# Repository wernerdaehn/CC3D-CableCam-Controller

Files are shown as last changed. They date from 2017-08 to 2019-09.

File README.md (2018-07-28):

[LICENSE](LICENSE)

# CableCam-Controller

**A CableCam Controller to allow smooth movements and automatic braking near the end points of the rope.**

## Goals

The most simple way to control a cablecam is by connecting the RC receiver to the motor controller (=ESC, electronic speed controller) and control it like a RC car.
But this has multiple limitations this CableCam Controller tries to solve:

1. The CableCam might crash into the start- or endpoint by accident. Would be much nicer if the CableCam calculates the required braking distance constantly and does engage the brake automatically. This way it stops no matter of the user input.
2. A smooth acceleration/deceleration makes the videos look more cinematic. Even when the stick is pushed forward at once, the CableCam should accelerate slowly instead of the wheel spinning damaging the rope.
3. A speed limiter to protect the CableCam from going too fast and for constant speed travels during filming.
4. Preprogram movement patterns and the Cablecam repeats them on request.

To achieve that, the CableCam controller sits between the receiver and the motor controller and acts as a governour of the receiver input. If, for example, the user did push the stick forward from neutral to max within a second, the CableCam Controller rather increases the stick position slowly. For speed and positional input the controller is connected to two hall sensors on one of the running wheels.

MCU used is [STM32F405RG](http://www.st.com/en/microcontrollers/stm32f405rg.html) 
Board used: Any CC3D Revolution or clone, e.g. the [Flip 32 F4](https://github.com/iNavFlight/inav/blob/master/docs/Board%20-%20Airbot%20F4%20and%20Flip32%20F4.md) which can be bought at various shops for little money [(here?)](https://www.rctech.de/flip32-f4-flight-controller.html).

See all videos at: https://www.youtube.com/channel/UCTLw_Boy24qAhuygCyIOzyw 

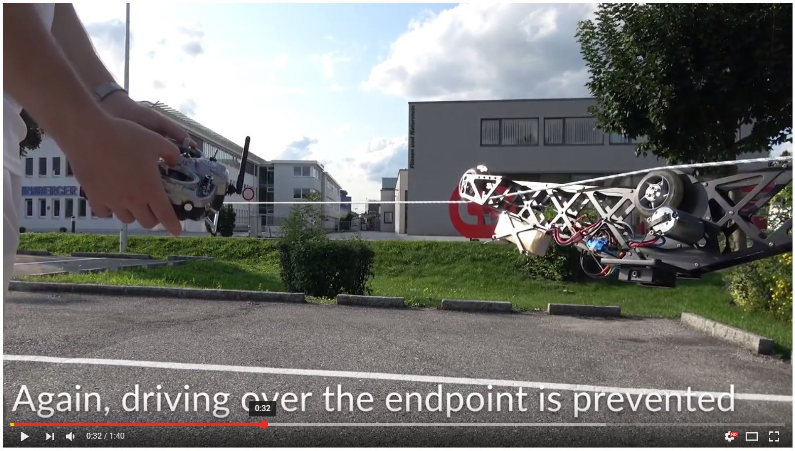
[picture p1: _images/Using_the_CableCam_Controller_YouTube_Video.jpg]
Using the CableCam Controller (https://youtu.be/ohzvkKzsO8Q "Using the CableCam Controller")


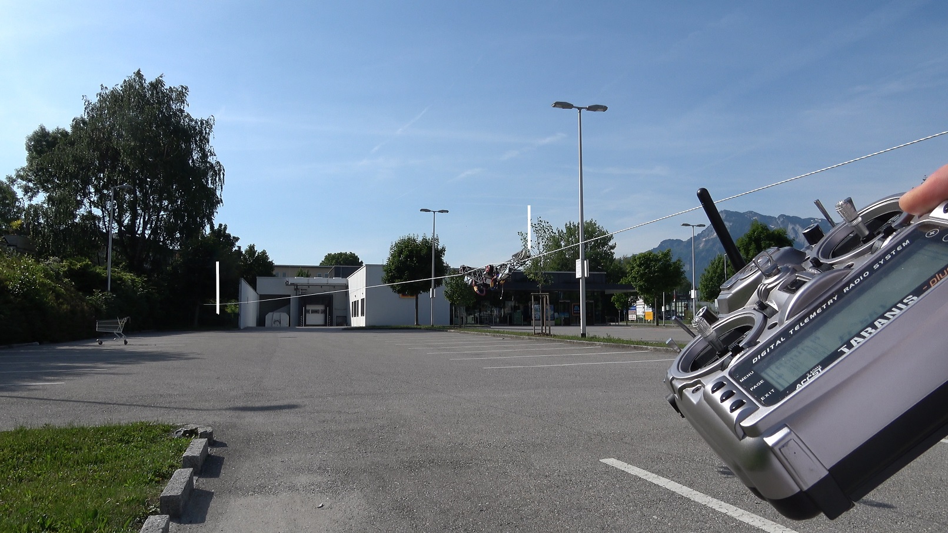
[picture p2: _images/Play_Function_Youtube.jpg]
The Play function (https://www.youtube.com/watch?v=D3UhXKbMN38 "The Play function")


If the stick is pushed full forward, the cablecam will start accelerating with the maximum allowed value instead until the maximum allowed speed is reached. This speed is held until it starts to decelerate with the same acceleration level so that it reaches the end point at zero speed.

Using the speed dial the maximum speed can be configured. And with the accel dial the steepness of the linear acceleration curve.

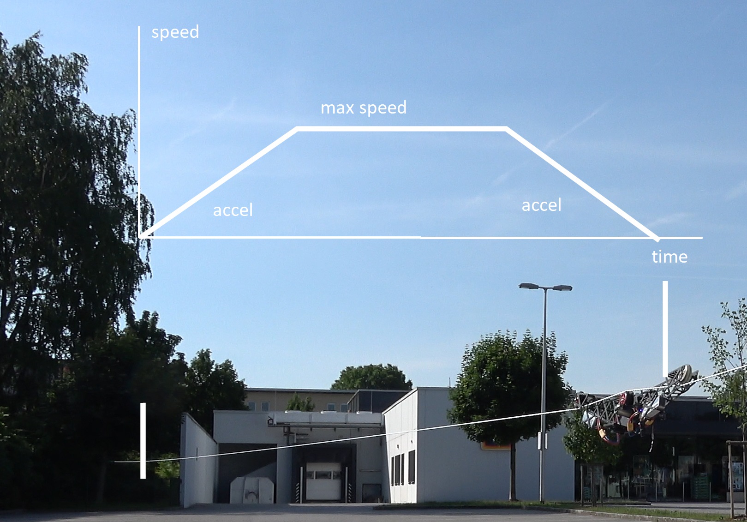
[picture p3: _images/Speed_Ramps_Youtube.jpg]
Speed Ramps (https://www.youtube.com/watch?v=Usq5xiH9H7Y)


## Setup

1. [Flashing the Firmware](docs/Step%201%20-%20Flashing%20the%20Firmware.md)
2. [Connecting the board](docs/Step%202%20-%20Connect%20to%20the%20board.md) to the computer for first tests and settings
3. Choosing the receiver
   1. [SBus](docs/Step%203a%20-%20Receiver%20Input%20SBus.md)
   2. [SumPPM](docs/Step%203b%20-%20Receiver%20Input%20SumPPM.md)
4. [Assigning input channels](docs/Step%203b%20-%20Receiver%20Input%20SumPPM.md)
5. Connecting the motor controller (ESC)
   1. Using a [servo signal to control the ESC](docs/Step%205a%20-%20Regular%20ESC.md)
   2. Using the [VESC6 as motor controller](docs/Step%205b%20-%20VESC%20as%20motor%20controller.md)
6. [Connecting the position sensor](docs/Step%206%20-%20Connecting%20the%20Position%20Sensor.md)
7. [Limiters](docs/Step%207%20-%20Limiters.md)
8. [Endpoints](docs/Step%208%20-%20Endpoints.md)
9. [Aux Channel](docs/Step%209%20-%20Aux%20channel.md) (optional)
10. [Bluetooth](docs/Step%2010%20-%20Bluetooth.md) (optional)
11. [Play Function](docs/Step%2011%20-%20Play.md) (optional)

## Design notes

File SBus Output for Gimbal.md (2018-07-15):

# SBus Output

In order to control the gimbal there are multiple options

- A second remote like the one that comes with the Ronin itself.
- A second receiver in case the RC sender supports two receivers being bound to it simultaniously. FrSky Taranis does.
- Split the SBus signal from the receiver.
- CableCam Controller itself does generate the SBus signal for the Gimbal.

The latter is described here. The longterm goal is to enable the cablecam controller fully automatic movements including gimbal. Repeat travel patterns, keep the camera pointing to a POI regardeless of where it is at the moment and things like that.

At the moment however the SBus input channels are mapped to output channels and a SBus signal is created for that.

## Hardware

#### MCU Pins used

| Function | MCU Pin | MCU Function | Connector Pin | Flip32 F4  |
| --- | --- | --- | --- | --- |
| SBus Out (non-inverted) | PC7 | USART6_TX | FlexIO Pin8 | CH6/TX6/J6 |
| GND | | | FlexIO Pin1 | GND/J2 |

Attention: **Do not connect the +5V line** with the board! Since both, gimbal and board do provide 5V power, it could cause damage. Would be like connecting two batteries with each other.

#### Pinout

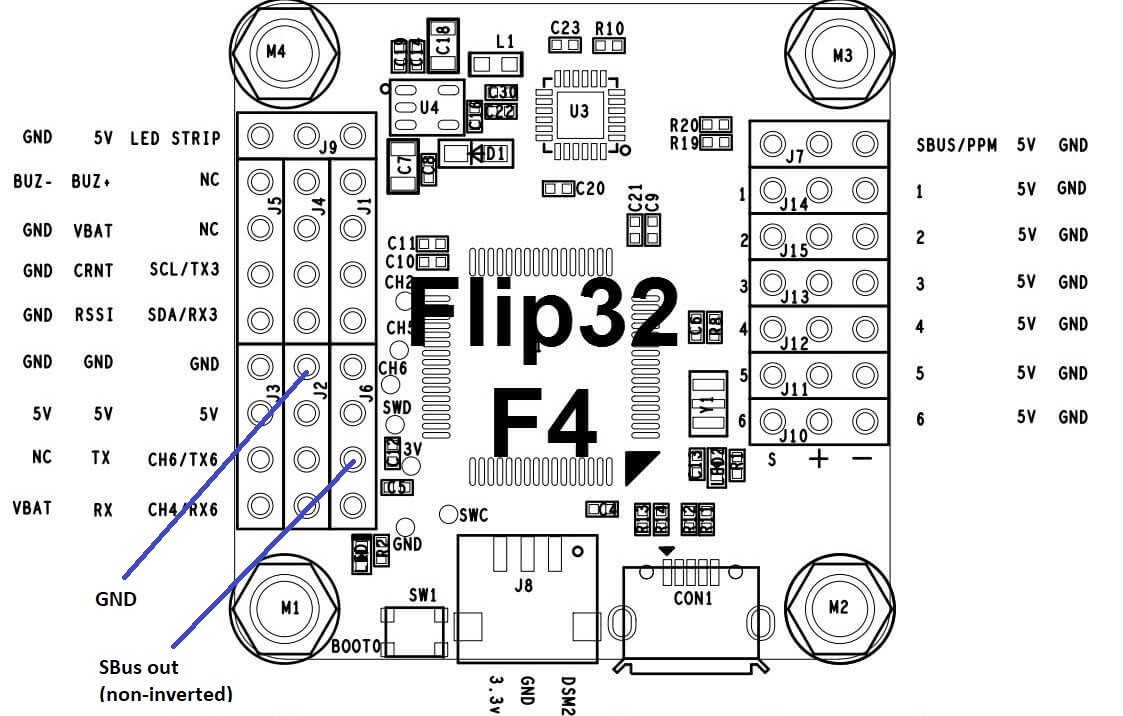
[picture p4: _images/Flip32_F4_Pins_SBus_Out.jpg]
UART Pins


Because the CC3D Revo does not have an output with a SBus inverter, this needs to be added externally. A search for "SBus Signal Inverter" shows many options, e.g. [this](http://flyingfolk.com/S-BUS-Receiver-Signal-Inverter-Converter-NAZE32-Flip32-SP3-Racing-Flight-Controller).

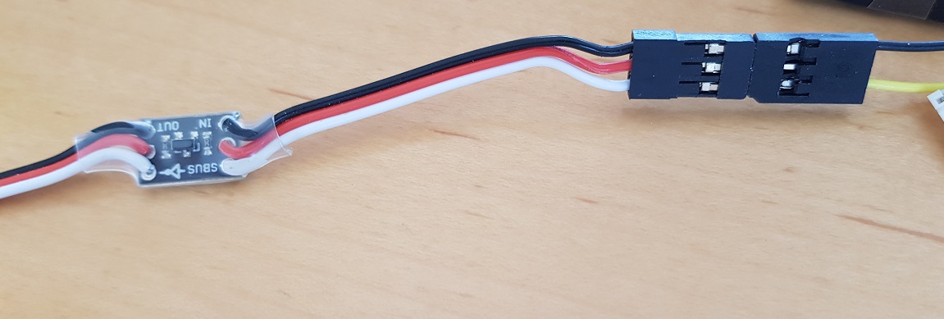
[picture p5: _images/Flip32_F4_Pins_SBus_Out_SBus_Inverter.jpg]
UART Pins


## Associated commands

| Command | Allowed values | Description |
| --- | --- | --- |
| \$G | | Print the current mapping |
| \$G \<channel 1\> ... \<channel 8\> | 1...16 or 256 to unmap | Set the channel mapping |
| \$n | | Note that the neutral range of the receiver input is used for the SBus output as well |
| \$D \<channel 1\> ... \<channel 8\> | integers | Set the SBus out default values in case they are not mapped  |

## Settings

The Ronin-M expects a (almost) fixed channel assignment, as seen in the DJI Gimbal assistant.

Usually the mapping is:

| Channel | Function | Note |
| --- | --- | --- |
| 1 | Tilt | can be configured in the DJI app |
| 2 | Roll | can be configured in the DJI app |
| 3 | | not used by the Ronin-M |
| 4 | Pan | can be configured in the DJI app |
| 5 | | not used by the Ronin-M |
| 6 | Function | left switch on the Ronin Sender |
| 7 | Mode | right hand switch on the Ronin Sender |
| 8 | | not used by the Ronin-M |

Note: In the DJI App the channel numbering starts with zero, not one.

Using the \$G command, the RC sender channels can be mapped to any of those for channels. For example the gimbal should be controlled with the left stick, channel 1 used for pan, channel 2 for tilt. The Function switch should be in the middle always ("Normal speed") and the Mode switch on upper ("Free, SmoothTrack Off").

In this case \$G 2 256 256 1 256 256 256 256 would be the correct setting.

| Ronin channel | Ronin | Input channel | $G value |
| --- | ----- | --- | --- |
| 1 | Tilt  | 2 (stick up/down) | 2 |
| 2 | Roll  | | 256 |
| 3 | | | 256 |
| 4 | Pan | 1 (stick left/right) | 1 |

As the Function and Mode is not assigned to a RC sender channel, it outputs the default values of neutral. For the Mode switch however it should be set to high. Hence the defaults are changed to

\$D 992 992 992 992 992 992 2000 992

If all needed channels are mapped, then the default settings are never used, e.g. \$G 2 8 256 1 256 6 7 256 would assign all five channels the Ronin-M does use to various channels of the RC sender.

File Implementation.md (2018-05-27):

## Getting started

### Hardware

Instead of using a custom build PCB, the project is based on easy to get hardware but flashed with a new firmware. 
This PCB should be small, have an onboard power regulator suited for RC-receiver typical voltages, servo connectors for power in and ESC output. It should also be based on a STM32F4 chip for easier flashing of the firmware - no bootloader needed - and include the needed hardware inverter for SBus signals. The Flight Controllers developed for Copters are an obvious choice.
In particular the [CC3D Revolution board](http://opwiki.readthedocs.io/en/latest/user_manual/revo/revo.html) is a perfect match. The only drawback of the CC3D Revo is that it contains additional hardware like a magnetometer, a barometric height sensor and an expensive RF link - nothing useful for a CableCam. But luckily there a clones of this board without these components, making the board cheaper as well.

_Note: The STM32F4 allows very flexible remapping of the pins to different functions, hence what is supposed to be used as output in the CC3D Revo firmware is rather used as input with the CableCam Controller firmware occasionally._

<a href="https://raw.githubusercontent.com/wernerdaehn/CC3D-CableCam-Controller/master/_images/CC3D_Revolution_Schematics.png">
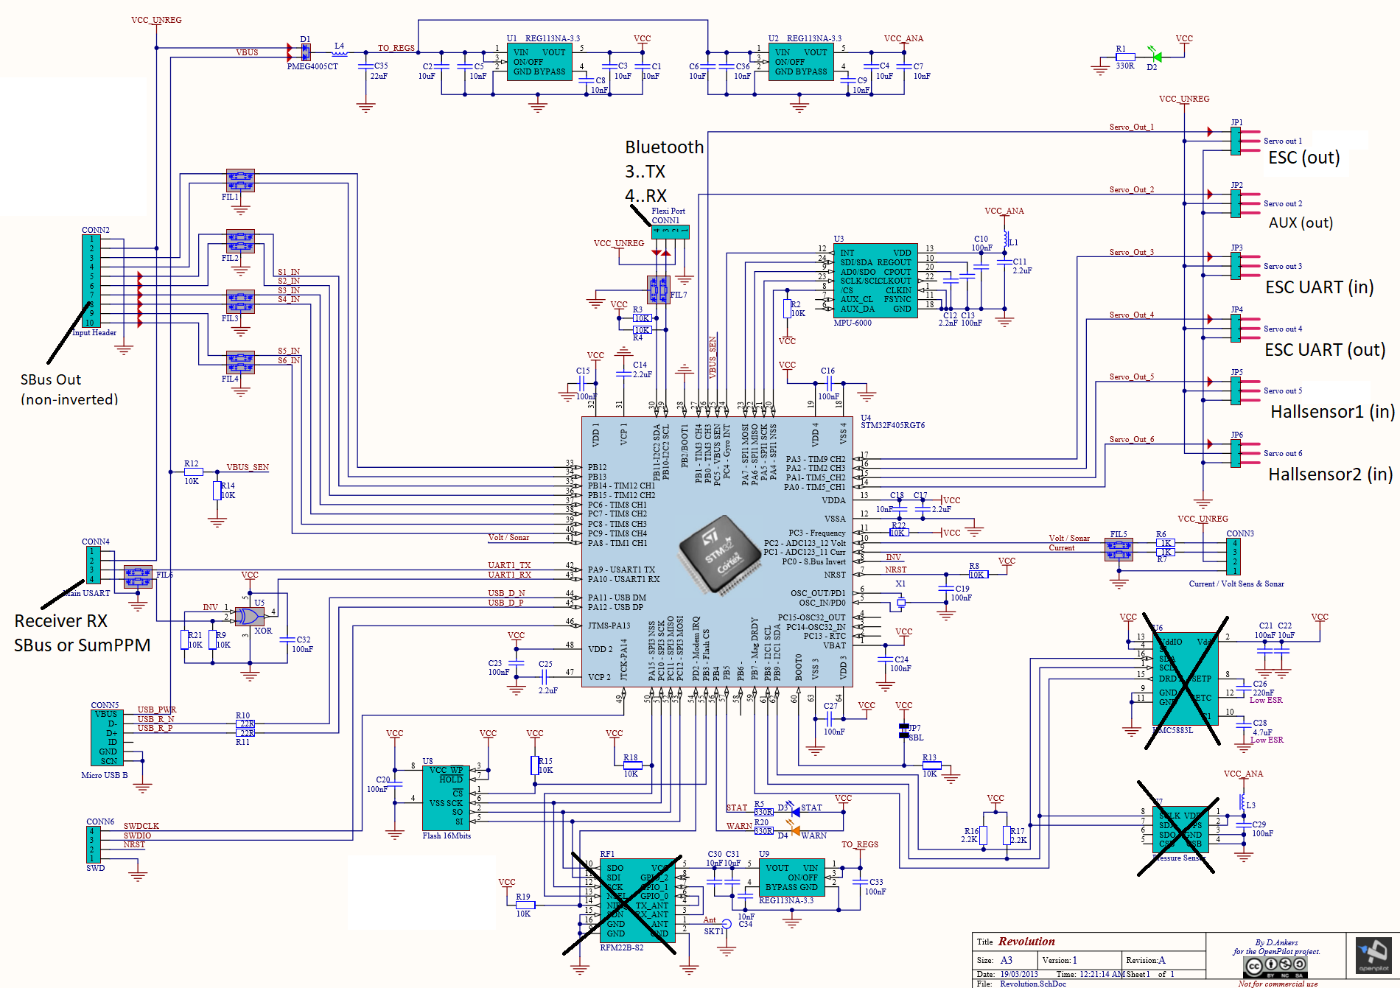
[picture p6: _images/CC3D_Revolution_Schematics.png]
  
</a>

As said, the board is put between the ESC and the receiver and gets the positional input from the hall sensors in addition.

<a href="https://raw.githubusercontent.com/wernerdaehn/CC3D-CableCam-Controller/master/_images/Hardware_Overview.jpg">
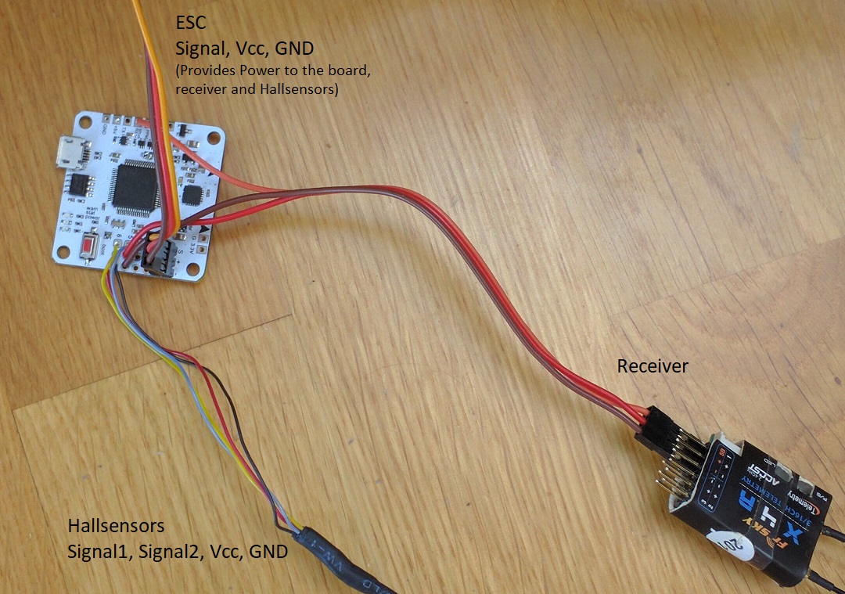
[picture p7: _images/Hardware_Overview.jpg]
  
</a>

The board can be powered via two methods, either via USB or via one of the Vcc_unreg pins on the Servo connectors. The USB power is applied to the board electronics only, hence is useful for flashing and configuration but not for powering the receiver. Also USB does not provide enough amps for the receiver. That is the reason the receiver and the hall sensors are not powered by the +5V pin but via the Servo out pins.
As the hall sensor is connected to Servo5 and Servo6 (order does not matter - can be swapped in the firmware) but needs Vcc and Gnd just once, the Reciver power cables are soldered to Servo5 Vcc and Gnd.
In other words, as in the normal case the ESC provides power to the receiver, just not directly but with the CC3D Revo board inbetween and hence powering it and all other external components as well.

_Note: All types of receivers are connected to the SBus/RX1 pin. The PPM pin is not used yet, not even for PPM receivers. The main reason is to make sure only one receiver can be connected._

<a href="https://raw.githubusercontent.com/wernerdaehn/CC3D-CableCam-Controller/master/_images/Board_with_Cables.jpg">
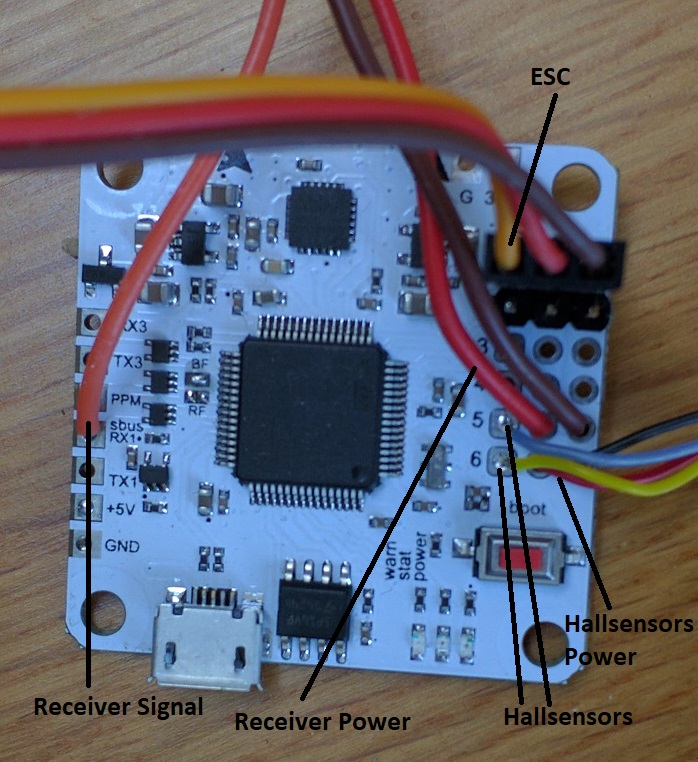
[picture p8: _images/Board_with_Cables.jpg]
  
</a>

#### Hall sensor

The hall sensor is very simple. The [Allegro Microsystems A1120](http://www.allegromicro.com/en/Products/Magnetic-Digital-Position-Sensor-ICs/Hall-Effect-Unipolar-Switches/A1120-1-2-5.aspx) sensor connects the output to Gnd if the magnetic field perpenticular to the chip surface exceeds a certain level and opens that switch if it falls below a level (=Open Drain). These two levels are different, hence avoiding noise in case the magnet field is exaclty at the switch level (=Hysteresis). As a result the sensor board can be very simple. Power between 3..24V is provided - hence perfectly suited for the Vcc_unreg provided by the ESC - and a capacitor nearby the chips is needed. The output signal of both is connected directly to the Servo5&6. A pullup resistor is not needed either, the STM32 MCU internal ones are turned on for those two pins.

<a href="https://raw.githubusercontent.com/wernerdaehn/CC3D-CableCam-Controller/master/_images/HallSensor_Board.png">
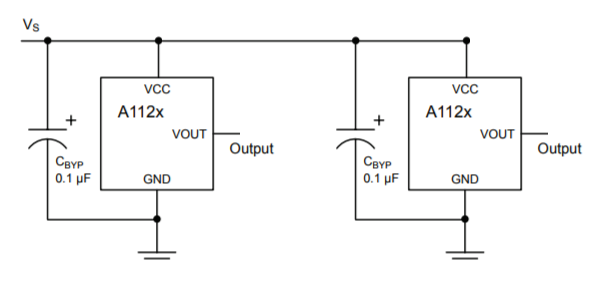
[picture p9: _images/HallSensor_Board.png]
  
</a>

The only important things to make sure are
1. The hall sensor does switch on and off reliably, meaning the magnetic field has to raise above and fall below the thresholds for sure.
1. The two hall sensors have a delay between switching on/off as this delay tells the rotation direction. If both would switch on exactly the same time, no rotation direction can be derived.

To achieve that one of the running wheels has 22 bores of d3x8mm (3mm drill and 8mm deep) and magnets are inserted alternating north/south. The hall sensor does switch on north magnetic fields only and therefore by adding a south orientated magnet between, it is an absolute certainty, the north field strength falls below the required level. 
In my case the bores are drilled into the skate wheel with a diameter of 60mm, hence the distance between each drill is 8.6mm. So as long as the distance between the two hall sensors is not 17.2mm or multiples thereof, they will not switch on/off at the same time. I aimed for a distance of 8.6mm+50% = 13mm roughly.

_Note: The sensor board PCB is currently redesigned using above guidelines. Maybe LEDs will be added as well as visual indication?_

### Flashing the firmware

One of the advantages of using a STM32F4 is that flashing got much more simple. No additional hardware is needed, no bootloader to be flashed first. The STM32F4 has an USB bootloader onboard already. All that is required is to have the boot button on the board pressed while powering it, and the bootloader is active. 
Then the ST provided DfuSe program is used to upload the firmware provided as _.dfu_ file in the bin folder of this project.
That's about it. In more detail, the steps are shown below.

_Note: All drivers used are included in a standard Windows 10 installation._
1. Install the ST provided DfuSe utility from the bottom of [this page](http://www.st.com/en/development-tools/stsw-stm32080.html).
1. Run the installed DfuSe program.
1. Connect the board to your computer via USB and while doing so, keep the boot button pressed. When the board is powered with the boot button pressed, the STM32 internal USB bootloader is started instead of the firmware.
1. As this activates the STM32F4 hardware bootloader and no firmware runs, only the red Power LED should be on. If the green Status LED does blink, the firmware is active. Try again above step.
1. Download the firmware from this project https://github.com/wernerdaehn/CC3D-CableCam-Controller/blob/master/bin/Debug/CableCamControllerF4.dfu
1. At the bottom of the utility, in the _Upgrade or Verify Action_ area, click on _Choose_ and select above's downloaded CableCamControllerF4.dfu file. 
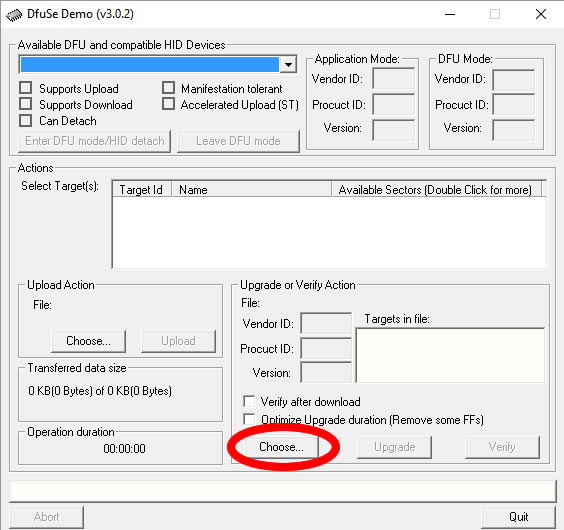
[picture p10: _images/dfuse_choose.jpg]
<br/>
1. The DfuSe Utility should show in the top box the text _STM Device in DFU Mode_. This indicates the board's hardware bootloader is running. 
1. If it does, the _Upgrade_ button copies the firmware onto the board. 
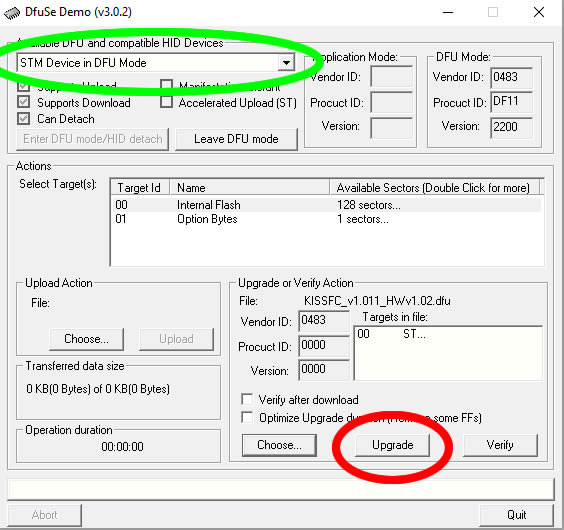
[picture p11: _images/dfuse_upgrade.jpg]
<br/>
1. The next dialog(s) is to be confirmed with _yes_. We are certain the firmware is for the STM32F405RG chip.
1. To validate the flashing truly was successful, the _Verify_ action can be triggered, just to doublecheck.
1. At the top, the button _Leave DFU mode_, does restart the device and as the boot button on the board is not pressed during startup, it will boot the firmware.
1. A first indication that everything is normal is when the yellow Status LED on the board does flash with 1Hz.

### Initial Setup and command reference

When the board is connected with a USB cable, a new virtual com port is created and commands can be sent to the board using a serial terminal.
Everything can be configured via commands and the current settings and states be read as well.
The format to enter commands is to start with a _$_ sign, followed by the program character, optional parameters and a final \r and/or \n char.
For example $h follwoed by the return key would print the help text.

The first thing to do is selecting the RC receiver type, SBus (1) or SumPPM (0..default). So enter the command _$I_ to see the current setting and _$I 1_ to switch it to SBus.
Using the command $1 invokes a guided setup of the input channels and hte neutral range with many sanity checks. Make sure the RC sender does output something on the desired switches and no mixers are enabled.

### Bluetooth
To simplify using the controller all settings can be done via bluetooth as well. It assumes the bluetooth module is connected to RX3/TX3 of the CC3D Revo and runs at 38400,8,n,1. In case the module is a HC-06, using the command _$B_ does everything to setup the module correctly, figuring out the current baud rate, changing it, give the module the name _cablecam_ and set the security Pin to 1234. 

### Command Reference

Command | Description
------- | -----------
_$1_ | Guided setup through for the receiver once _$I_ was used to select the receiver type. This command sets the same values as _$i_ and _$n_ does.
_$a_ | Shows the two acceleration values, the first is the max acceleration in operational mode, the second in programming mode
_$a int int_ | sets the two acceleration values. Default is _$a 20 10_
_$A int int int_ | sets the neutral point and range and maximum deflection. The default _$N 1500 0 700_ creates a pwm signal with a puls width of 1500us in neutral and +-700us without a neutral range.
_$b_ | Print a long hex string with the current settings encoded in them. Useful as a backup and to transfer the settings to another board.
_$b string_ | To write all settings as encoded in the string.
_$B_ | Configure the HC-06 bluetooth module connected to RX3/TX3 pin
_$e_ | Print the maximum eRPMs as defined in the VESC ESC.
_$e int_ | Set the maximum eRPMs as defined in the VESC ESC.
_$E_ | print the status information of the VESC.
_$g_ | Print the maximum positional error before going into an emergency brake. In case moving the stick slowly towards neutral does not apply enough brake power and hence the endpoint will be overshot by more than this value, the ESC output is reset to neutral. Thus applying the maximum brake power the ESC can apply. Default is 100 hall sensor steps.
_$g int_ | Set the max error.
_$G int1 .. int8_ | The controller can output a (non-inverted) SBus signal meant for the DJI Ronin gimbal. Which input channel should be assigned to channel 1 to 8?
_$i_ | Print the the current channel assignments and a overview of all channels with their current values as received from the RC receiver. A value of 0 means no valid data received.
_$i int1 .. int8_ | Assign the input channels to functions in the order of speed, programming switch, endpoint button, max acceleration dial, max speed dial, mode selector, Aux Channel, Play switch input. A value of 256 is allowed in order to disable those RC functions.
_$I_ | shows which type of receiver signal is expected, SumPPM or SBus.
_$I 0_ | SumPPM receiver is connected.
_$I 1_ | SBus receiver is connected.
_$j char | Prints the channel assignment of a specific function. Characters can be v (=speed), m (=Mode switch), P (=endpoint programming), e (=end point tip switch), A (=max accel dial), V (=max speed dial), a (=Aux input), p (=play switch).
_$j char int | Set a channel to a specific function. Allowed values for char see in the line above.
_$m_ | print the operation mode
_$m 0_ | Positional mode. In this mode the stick moves a target position and a PID loop does everything in order to keep the CableCam as close as possible to that point. ATTENTION: Not tested, do not use.
_$m 1_ | Passthrough mode. Essentially output = input. All the control does is converting the receiver signal into an ESC servo output signal. Useful for testing and to calibrate the ESC for neutral/max/min points.
_$m 2_ | Passthrough with speed limits. The stick movements is filtered through the acceleration and speed filter, thus being turned into a ramp. Enpoints are not considered.
_$m 3_ | Passthough with speed limits & end points. In addition to the _$m 2_ mode, the end points are considered as well. The default mode, the mode that should be used all the time.
_$n_ | Prints the neutral point of the input, the neutral range and the 100% range. Make sure that the neutral point is the same value _$i_ shows for the speed channel when the RC stick is in idle.
_$n int int int_ | set the neutral point to the first value and the neutral range to the second. The third value is the maximum deflection from neutral. The default value of _$n 992 30 800_ would consider all stick values from 962 to 1022 as idle and values from 162 to 1762 as thrust.
_$N_ | Prints the neutral point and range of the ESC output pwm signal. 
_$N int int_ | sets the neutral point and range. The default _$N 1500 30 700_ creates a pwm signal with a puls width of 1500us in idle and to create movement overcomes the neutral range of the ESC by starting with 1530 (or 1470 for reverse). And 100% speed would be an output signal of 2230 and 770 in reverse. This should match the defaults of the ESC but running an ESC calibration is advised.
_$p_ | Print the low endpoint, the high endpoint, the current position and the current speed via two methods.
_$P_ | Turn on the Play function for the next few seconds. Hence this command has to be sent constantly to keep the play program running.
_$r_ | Print the rotation direction, clockwise (+1) or ccw (-1). This is important information once the cablecam did overshoot the endpoint. Then the controller allows driving back into the allowed range but not further outside. A value of 0 means it has not been set yet.
_$r int_ | Sets the rotation direction.
_$S_ | Print a summary of all settings.
_$v_ | Print the max value the speed input signal is allowed range between the neutral point. With the neutral point at 992 and a speed limit of 800, the full SBus range of 192 to 1792 can be used. With a value of 400, everything above 50% thrust on the stick is limited to 50% max thrust. Note that this value controls the stick and hence is dependant on the type of input receiver.
_$v int int_ | Sets the max speed for the operational mode and the programming mode. The idea is to limit the max speed when setting the endpoints as a safety precaution. Default is _$v 500 100_.
_$V_ | prints the current firmware version.
_$w_ | Write all active settings to the EEPROM from which they are loaded at boot time.
_$x_ | Print the exponential factor for the thrust stick input.
_$x double_ | Set the exponential factor for the thrust input curve. A common input curve is a linear relationship between the stick position and the output signal. 100% stick means 100% output, 50% stick is 50% ouput signal. This behavior would require the factor to be set to 1.0. If the stick can send signals in 0.1% steps and the maximum RPMs are 50'000, the lowest possible resolution would be in 50RPM steps. Which is absolutely fine at higher speeds but at low speeds it does not allow fine control. The closer this factor is to zero, the fine grained low speeds can be controlled.

### The acceleration and speed limiter

When driving an RC car, applying full thrust instantly is fun, as the wheels start spinning, dirt flying through the air. For the CableCam not so much. Here a constant acceleration is more important. Therefore the CableCam Controller has in ramp built in.
As long as the user stays within the acceleration limit, he has full control. But if he exceeds the acceleration by e.g. pushing the stick forward too quickly, the stick movement is limited to the maximum allowed acceleration. So the acceleration limiter works by using the stick raw position, e.g. 50%, then apply the expo factor and that is the current stick input in percent. This value change is governed by the acceleration limiter.
The speed limiter works on the output instead. If the max speed is limited to 50%, the the VESC max erpm or the servo output signal is only 50% of what it has been configured as absolute max via _$e_ or _$N_. 

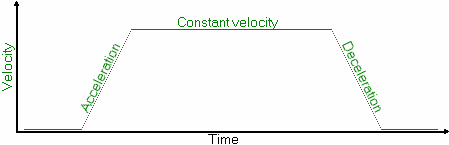
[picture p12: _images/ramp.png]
ramp


### Endpoint limiter

Using the programming switch the CableCam can be brought into a mode where the enpoints are set. Driving the CableCam to the startpoint and pressing the end point switch makes the current position the start point limit. The driving forward or reverse to the end point and pressing the end point switch a second time, set this as the second limit. 
When the programming switch on the RC sender is put back into the operational mode, the CableCam can be driven only within those two points.

To change the end points, the programming mode is entered again and the CableCam allows driving to any position, even outside of the previous set range. The sequence is always the same, first click after entering the programming mode sets the first point, all subsequent clicks modifes the second end point.

The logic for the end point limiter is a bit tricky. 
Based on the stick position and the acceleration limit, the time to zero is calculated. For example, if the stick is at position +100 and the acceleration is 20, it takes 100/(20*0.1)=50 cycles to reach zero. At a refresh rate of 20ms, 50 cycles are 50*20ms, that is one second. In other words, the cable cam should stop within one second.
From the hall sensor the controller knows the current speed, the time to stop from the stick level, hence the distance to stop can be calculated: s = v * t / 2 [(velocity-time graph)](http://www.bbc.co.uk/education/guides/z3bqtfr/revision/5).

This calculation is made in absolute numbers to simplify things. Which end point should be considered depends to the stick position only. If the stick is in forward direction, the current position plus the braking distance needs to be smaller than the end point. If the stick is in reverse, the position minus the braking distance has to be larger than the start point.
As soon as the calculation shows the end point will be overshot, the stick is moved towards the neutral position usng the max acceleration.
For a closed loop ESC this would cause the motor to actively engage the brake until the reduced target speed has been achieved. 
A regular car ESC does slow down less. Almost nothing in fact. The drag brake does kick in if the stick is in neutral only. 
Therefore a second test is performed, checking if the end point would be overshot by more than 100 steps - about 1m. If yes, although the stick value is constantly removed, the ESC signal is reset to neutral to engage the drag brake. 
That is the best the controller can do.
And as a second precaution, as soon as the end point was overshot, the stick is forced into neutral, causing the CableCam to stop as quickly as possible.

## Detailed Usage

## Development

### Hardware Mapping

Connector Pin | Description | MCU Pin | MCU function
------------- | ----------- | ------- | ------------
Servo1 | Servo Output to the ESC; Connect the ESC to it in order to feed it with valid PPM servo signals | PB0 | TIM3_CH3
Servo2 | Servo Output for Aux Input | PB1 | TIM3_CH4 
Servo3 | ESC Output via UART | PA3 | USART2_RX
Servo4 | ESC Output via UART | PA2 | USART2_TX
Servo5 | 32Bit Quadruple Encoder used for Hall Sensor input | PA0 | TIM5_CH1
Servo6 | 32Bit Quadruple Encoder used for Hall Sensor input | PA1 | TIM5_CH2
LED Status | Status LED on the boards (Low = On) | PB5 | GPIO
LED Warn | Warn LED on the board (Low = On) | PB4 | GPIO
MainUSART | Receiver input; In SBus Mode | PA10 | USART1_RX
MainUSART | Receiver input; In SumPPM Mode | PA10 | TIM1_CH3
IMU | SPI for MPU-6000 IMU | PA4 | SPI1_NSS
IMU | SPI for MPU-6000 IMU | PA5 | SPI1_SCK
IMU | SPI for MPU-6000 IMU | PA6 | SPI1_MISO
IMU | SPI for MPU-6000 IMU | PA7 | SPI1_MOSI
EEPROM | SPI for Flash 16MBit and optional RF Module (not used) | PA15 | SPI3_NSS
EEPROM | SPI for Flash 16MBit and optional RF Module (not used) | PC10 | SPI3_SCK
EEPROM | SPI for Flash 16MBit and optional RF Module (not used) | PC11 | SPI3_MISO
EEPROM | SPI for Flash 16MBit and optional RF Module (not used) | PC12 | SPI3_MOSI
EEPROM | Select for Flash 16MBit | PB3 | GPIO
Bluetooth | TX3 on Flexiport on Conn1 | PB10 | USART3_TX
Bluetooth | RX3 on Flexiport on Conn1 | PB11 | USART3_RX
SBus Out (non-inverted) | Pin 7 on FlexIO, Connect an inverter and control the DJI Ronin with that | PC7 | USART6_TX

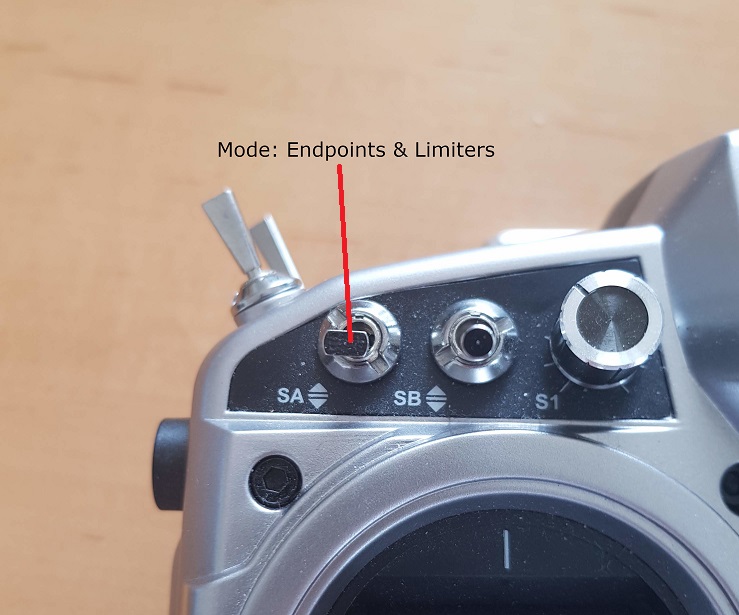
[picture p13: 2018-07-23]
_images/RC_ModeSwitchENDPOINT.jpg

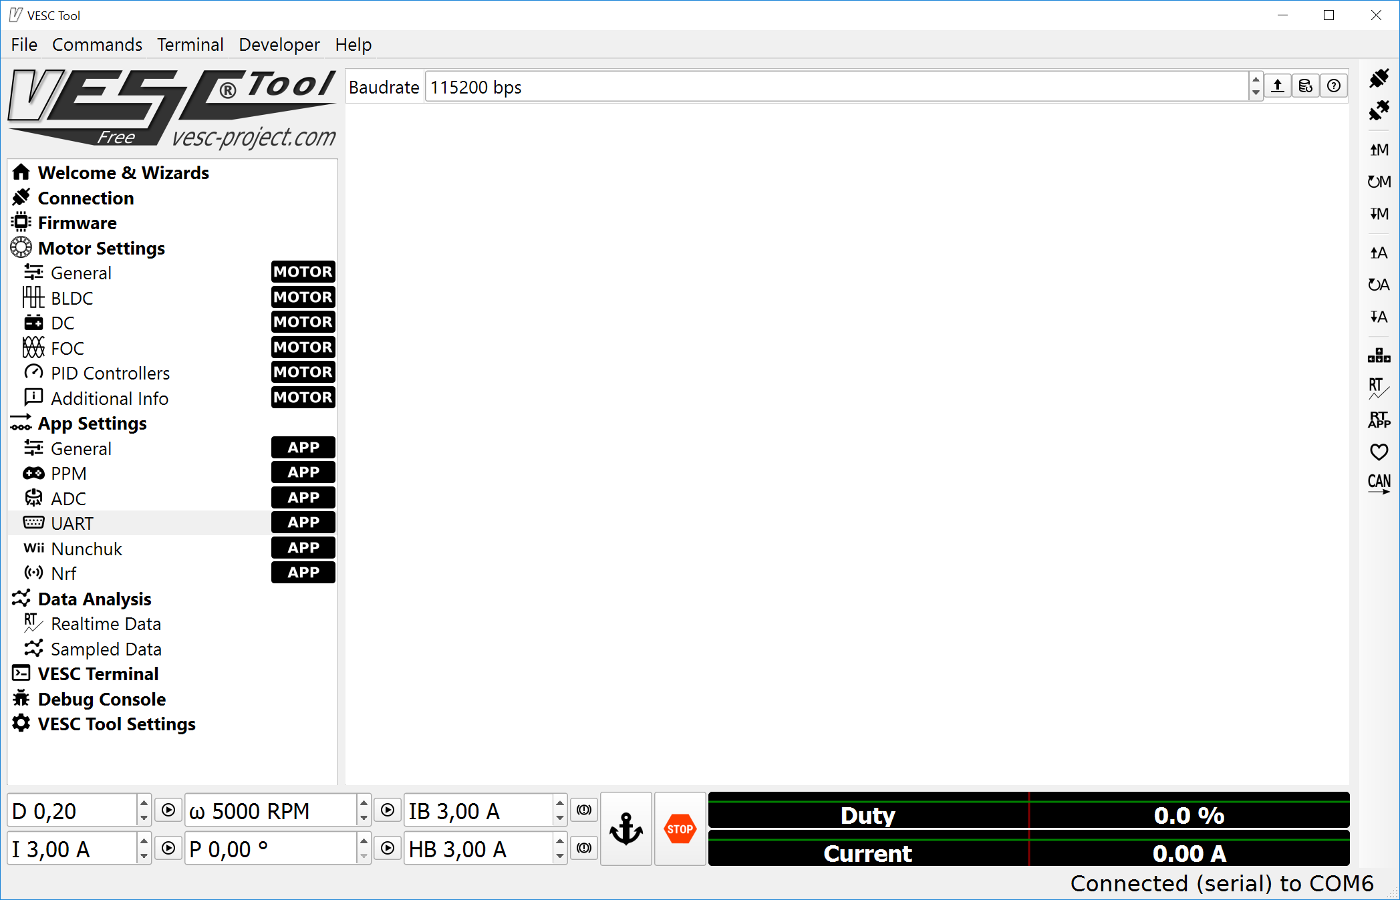
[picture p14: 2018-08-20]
_images/VESC_7_Baud.png

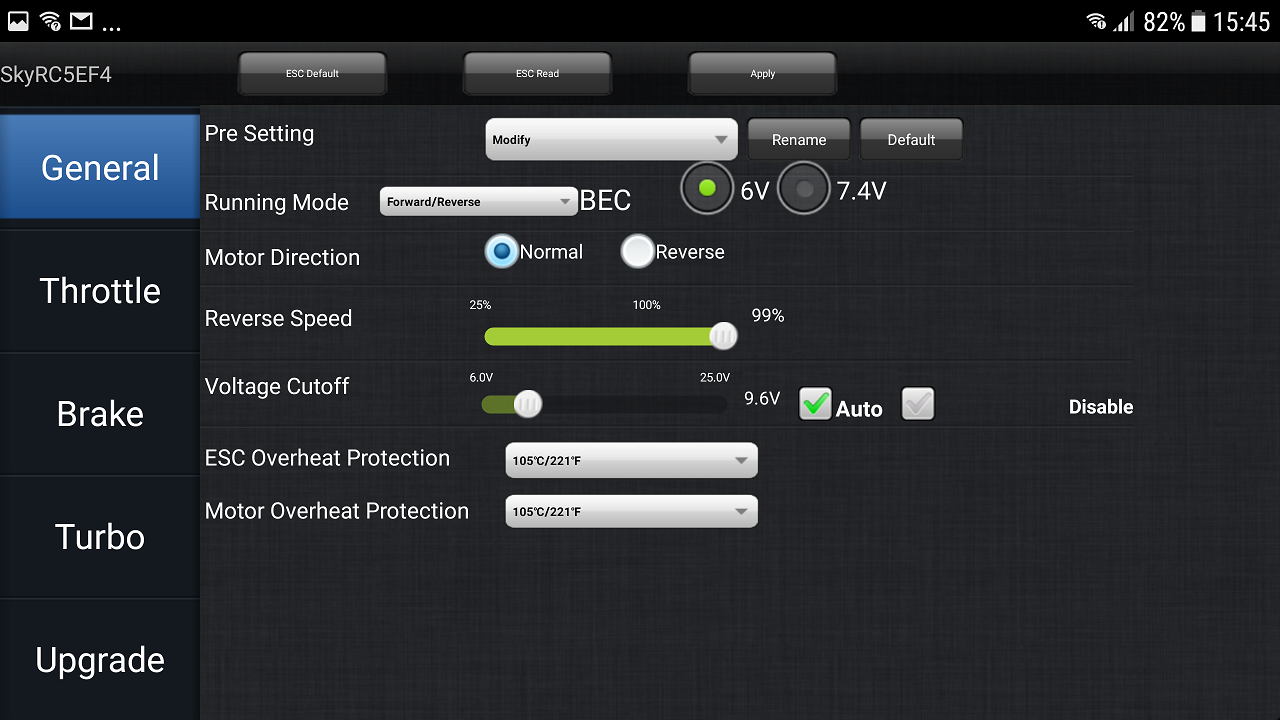
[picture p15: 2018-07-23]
_images/ESC_curves.png

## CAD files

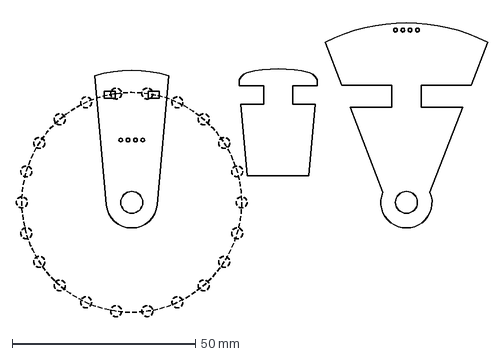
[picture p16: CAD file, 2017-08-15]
Sensorboard.dxf
128.7 x 82.0 mm

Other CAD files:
Sensorboard.3dm
Sensorboard.dwg

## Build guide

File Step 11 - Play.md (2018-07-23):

# Play Function

The controller also allows driving between the end points automatically, either by sending the \$P 1 command frequently or using a switch on the TX.

See this [video](https://www.youtube.com/watch?v=D3UhXKbMN38):

The Play function (https://www.youtube.com/watch?v=D3UhXKbMN38 "The Play function")

This mode is allowed only in strict conditions for:

- End points are set
- Mode is Limiter with Endpoints
- Speed Stick is in neutral
- ESC direction is set (\$r return 1 or -1 but not 0)
- Play was in Off before (else the cablecam might start moving when turning it on)

If one of these preconditions are not met, the controller falls out of the Play mode and Play has to be turned off and on again.

While the Play is running, the acceleration and speed limiters can be modified.

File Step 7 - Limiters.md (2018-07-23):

# Limiters

When driving an RC car, applying full thrust instantly is fun, as the wheels start spinning, dirt flying through the air. For the CableCam not so much. Here, a constant acceleration is more important. Therefore the CableCam Controller has in ramp built in.
As long as the user stays within the acceleration limit, he has full control. But if he exceeds the acceleration by e.g. pushing the stick forward too quickly, the stick movement is limited to the maximum allowed acceleration. So the acceleration limiter works by using the stick raw position, e.g. 50%, then apply the expo factor and that is the desired speed in percent. This speed-change is governed by the acceleration limiter.
The speed limiter works on the output. If the max speed is limited to 50%, the the VESC max erpm or the servo output signal is only 50% of what it has been configured as absolute max via _$e_ or _$N_. In other words, 100% throttle would create a 50% output signal only in this example.

ramp

### 

## Associated commands

| Command | Allowed values | Description |
| --- | --- | --- |
| \$a | | Print the current acceleration limiter |
| \$a \<decimal\> \<decimal\> | \>=0.001 and \<=1.0 | Set the acceleration limiter |
| \$v | | print the current speed limiter |
| \$v \<decimal\> \<decimal\> | \>=0.1 and \<=1.0 | Set the speed limiter |

When programming the end points, the cablecam should move slower probably. Therefore both commands require two parameters. First the value for the normal movement, second for endpoint programming.

## Settings

### Preconditions

The limiters are applied only in case the current mode (\$m or the TX switch - if configured) is not Passthrough. 

And, as said above, there are two limits. During EndpointProgramming the second parameter applies, else the first parameter.

### Speed Limiter

In order to drive with a constant speed or to limit the speed to prevent accidents, the output signal can be limited. A speed limiter of 50% would mean putting the stick at full forward, creates an output signal of 50% at max. So the servo signal would be (assuming \$N 1500 0 700) limited to +-350us (pulslength 1150us to 1850us), the VESC (assuming a max speed of \$e 50000) would get speed commands up to +-25000eRPMs.

If a dial on the TX is assigned to act as a speed limiter, then the configured value (via \$v) can be changed between 0.1 and this value. See the [RC Input Channels](Step 4 - Assigning Input Channels.md). 

In other words, the \$v value acts as the absolute maximum and the dial can be used to reduce that for the moment.

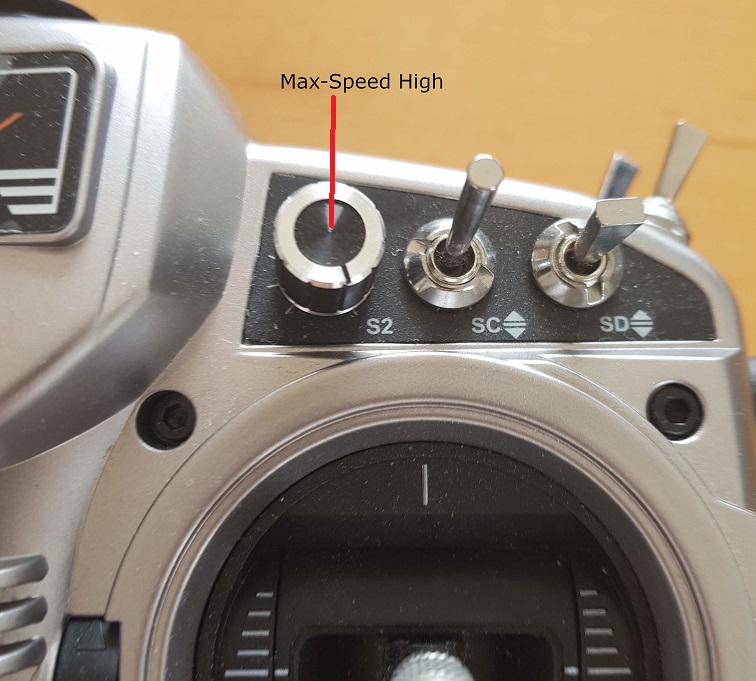
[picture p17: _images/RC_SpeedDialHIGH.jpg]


### Acceleration Limiter

For an even acceleration and hence professional looking shots, the acceleration limiter is used. Its value tells how much [percent] the stick can change per second. A value of 0.1 for example limits the change to 10% per second, in other words, it takes 10 seconds (= 1/0.1) from rest to 100%. And vice versa. The setting works on acceleration and deceleration identically.

As with the speed limiter, the acceleration limiter can be set via a command, \$a in this case, and the dial on the TX - if configured - can be used to select an acceleration limit up to this value.

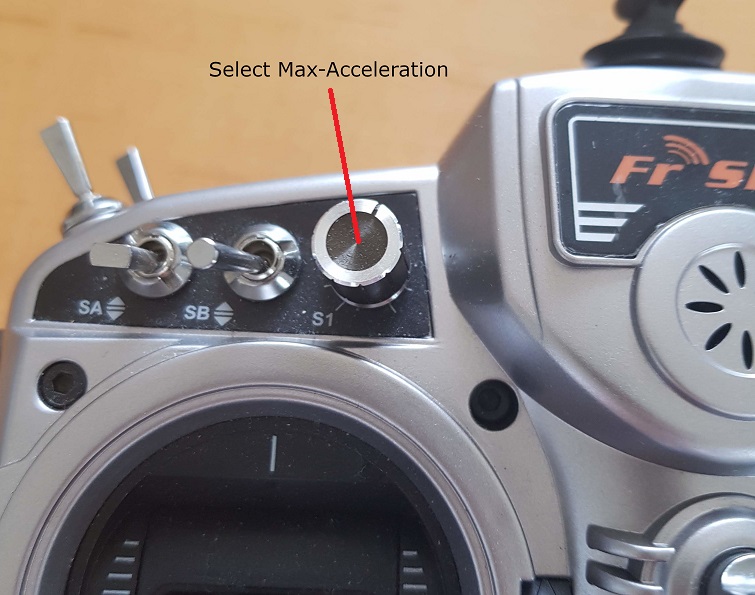
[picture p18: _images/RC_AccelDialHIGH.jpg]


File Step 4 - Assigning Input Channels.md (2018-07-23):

# Assigning Input Channels

The most important functions and settings should be controlled via the RC sender. As the sender can be programmed freely and functions should be assigned to match the personal preferences, this assignment is totally flexible.

Hence the first step will be to decide what functions to use and program the RC sender accordingly.

In this example, it is an **example** only(!), the RC sender has been programmed like this:

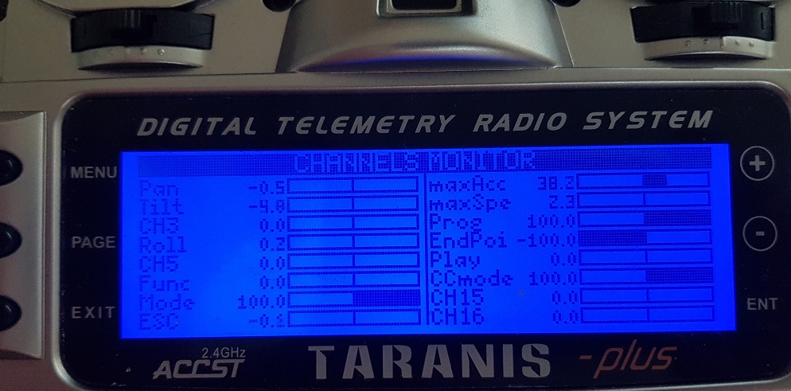
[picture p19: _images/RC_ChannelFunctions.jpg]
Channel Assignments


| Function | Example Channel# | Description |
| --- | --- | --- |
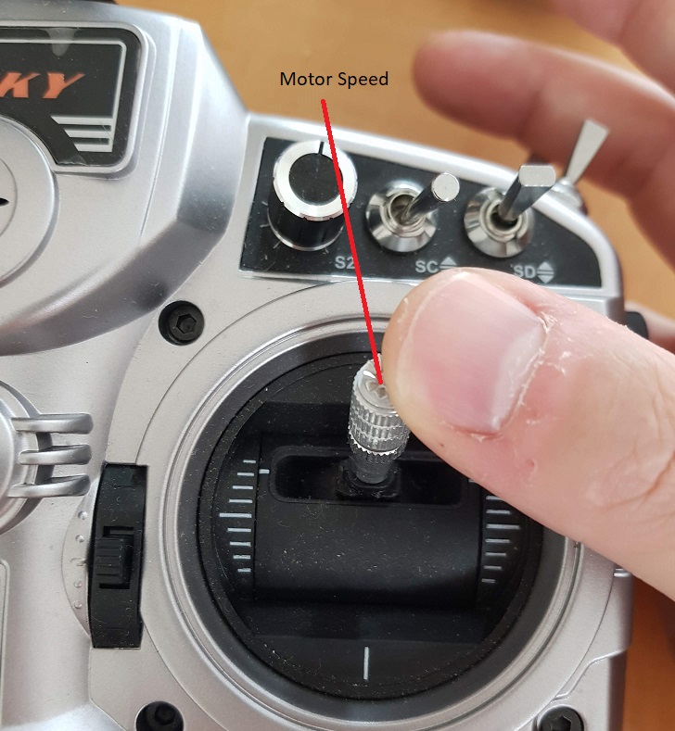
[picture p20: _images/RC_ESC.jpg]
| **ESC**  | 8 | Controls the CableCam speed |
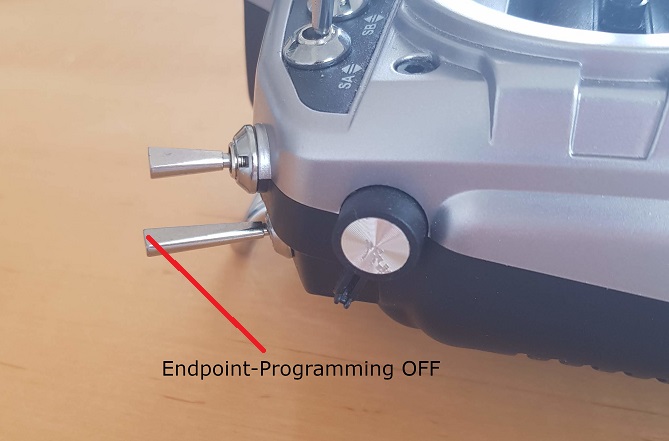
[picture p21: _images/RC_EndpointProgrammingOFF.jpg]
EndPoint
| **Prog**  | 11 | Endpoint Programming switch, flip to change from OPERATIONAL to ENDPOINT PROGRAMMING |
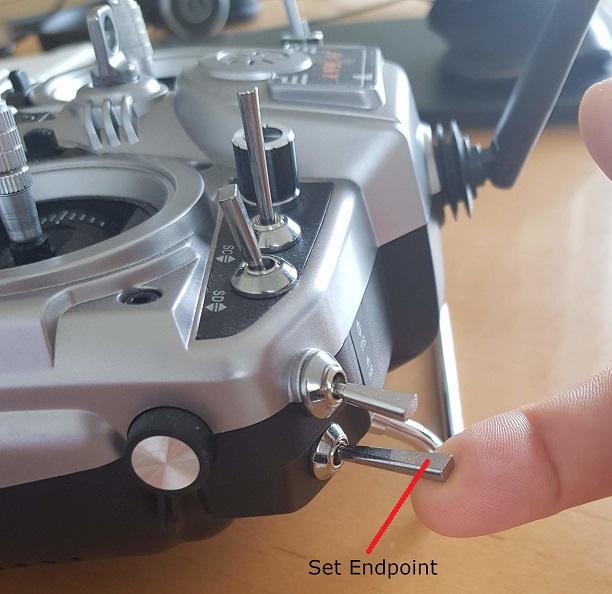
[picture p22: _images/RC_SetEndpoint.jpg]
EndPoint
| **EndPoint**  | 12 | A tip switch, when touched sets the current position as start/end point |
| **MaxAccel** Dial1 | 9 | A dial that allows changing the maximum acceleration |
| **MaxSpeed** Speed | 10 | A dial that sets the max speed at stick 100% |
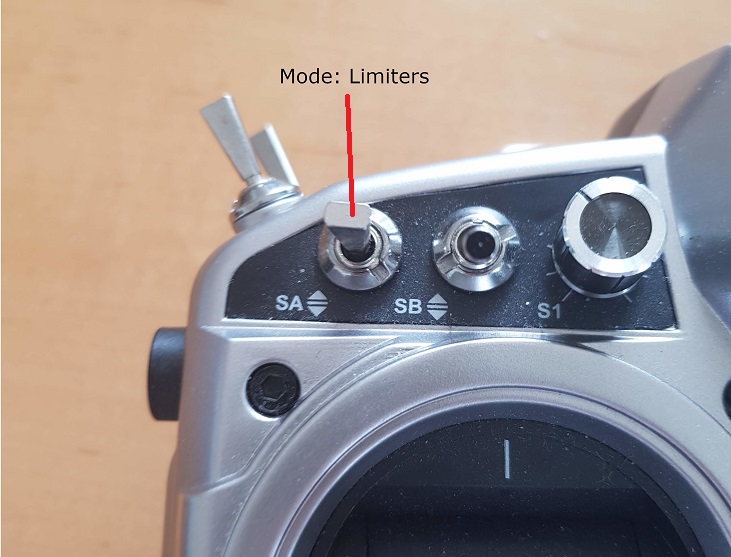
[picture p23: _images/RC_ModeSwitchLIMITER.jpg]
CCmode
| **CCMode**  | 14 | A three-way switch to change between Passthrough, Limiter and Enpoint-with-limiters operation mode |
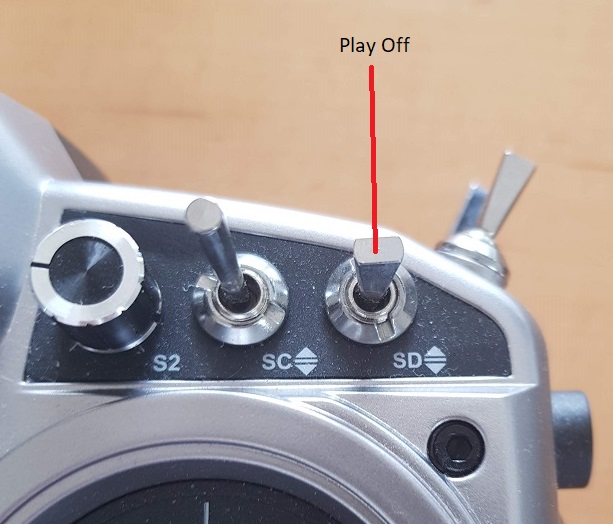
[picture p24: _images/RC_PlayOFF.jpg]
Play
| **Play**  | 13 | Allows the controller to move the cablecam between the end points automatically |
| **Aux** | | Servo #2 output can be controlled via a channel as well |
| **Gimbal** | 1 to 7 | Channels to control the gimbal |

## Associated commands

| Command | Allowed values | Description |
| --- | --- | --- |
| \$1 | | A guided setup |
| \$i | | print the current channel assignments |
| \$i \<ch#1\> \<ch#2\> ... | 1-16 or 256 | Set channel assignments |
| \$j \<char\> | v..speed<br />m..CCMode<br />P..Endpoint prog switch<br />e..Endpoint set tip switch<br />A..Max accel dial<br />V..Max speed dial<br />a..Aux source<br />p..Play switch | print the channel for a specific function |
| \$j \<char\> \<ch#\> | above char plus a channel source of 1-16 or 256 | set a source channel to a function, 256 clears it |
| \$n | | print the value ranges for the input |
| \$n \<neutral\> \<neutral range\> \<max deflection\> | neutral: 500-2000<br />neutral range: 0-100<br />max deflection: 300-1400 | set the value ranges for the input channels |
| \$x | | print the expo factor |
| \$x \<decimal\> | \>0.0 and \<=1.0, default: 0.1 | set the expo factor |

## Guided Setup

The most convenient method to setup everything is using the \$1 command. It reads the receiver input, sets the neutral point, range and max deflection and asks to change the input by using the sender, e.g. moving the speed stick to assign the channel to the speed function.

See <a href="https://youtu.be/UbZSGKW4F94">this video (here)</a> to get the idea.

This guided setup can be repeated many times until all desired channels are assigned to the various functions. (Or the manual setup can be used for all/for the missing functions)

Once the channels are assigned, it is probably a good idea to store all settings permanently using the \$w command.

## Manual Setup

With the guided setup above only the most important functions can be assigned. For setting all functions at once \$i is the best command. And to assign source channels to specific functions, the \$j command is meant for.

The \$i command also helps to get a quick overview of the assigned channels.

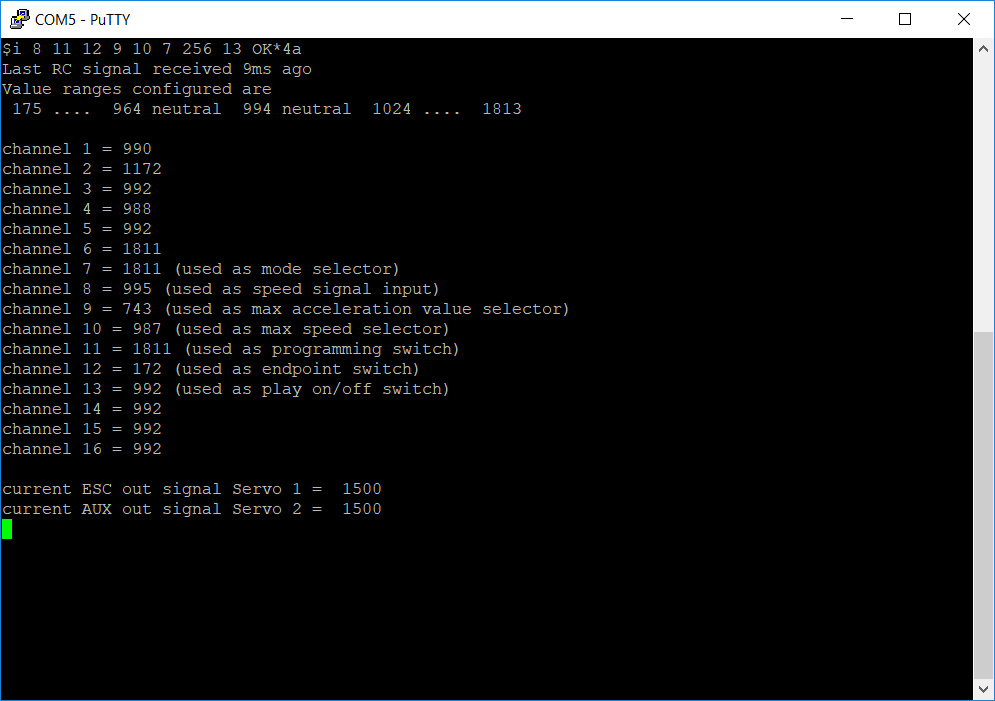
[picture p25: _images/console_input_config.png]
Input channel command


At the top it shows the information when the last signal was successfully decoded. 

The neutral range in a readable form, here the assumed values being received range from 175 to 1813 with 994 being the neutral point and everything between 964 and 1024 is considered neutral, hence no motor movemement within that range. This obviously has to match the values the receiver does send.

At the bottom the current output values for Servo1 (ESC Out) and Servo2 (Aux Out) are shown.

## Troubleshooting

- The \$i command shows zero values for all input channels.
  - This says that no valid signals are received. Reasons we have encoutered were
    1. The RC sender is not turned on or not bound to the receiver. The FrSky receiver does not return any output under these conditions, not even the default values it outputs when the connection has been lost.
    2. The input type is wrong. See \$I for SumPPM versus SBus.
    3. The receiver is not connected properly. Check if the receiver signal goes into the proper pin on the board, the receiver is connected via GND with the board and the receiver is powered.
  - For debugging, the pages for [SumPPM](Step 3b - Receiver Input SumPPM.md) and [SBus](Step 3a - Receiver Input SBus.md) have some methods described.
- The guided setup complains that more than one channel has been moved.
  - When moving a stick in one direction, of course it will wiggle a bit into the other direction as well. Therefore this error means that the other channel moved a lot. If the TX has a screen where the exact channel outputs are shown, this might proof that there is a misconfiguration in the sender, usually a mixer is active still.
- One of the switches is not recognized.
  - The TX has much more controls than available channels, therefore the most need to be assigned in the TX before they can be used.

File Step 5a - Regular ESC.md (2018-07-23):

# Using a regular ESC

The project started with regular ESCs as found in 1:8th scale buggies, rock crawlers to be more precise. These provide a lot of power for a decent amount of money but cannot be controlled as directly. The result is good but not perfect.

The minimum requirements for an ESC to be used are

- Supports Drag Brake - when put in neutral it should brake significantly
- Supports Initial Brake - it should brake even at low speeds, else it rolls down a hill faster and faster
- Supports a Forward/Reverse mode, not something where putting the stick into reverse does brake, once the car stopped in can be driven in reverse.
- Reverse can be 100% of forward
- Reverse and Forward use the same throttle curve
- Sensored motor and ESC

ESCs that are meant for Rock Crawlers usually do support all of the above but with linear throttle curves only.

A cheap ESC I use at the moment is the [SkyRC TS160](http://www.skyrc.com/index.php?route=product/product&product_id=212) for 3s batteries together with a [programming box](http://www.skyrc.com/index.php?route=product/product&product_id=176).

One that looks very promising is the [Hobbywing Xerun AXE](http://www.hobbywing.com/goods.php?id=635), at least once it is available for larger than 1/10th applications.

## Hardware

#### MCU Pins used

| Function | MCU Pin | MCU Function | Connector Pin | Flip32 F4  |
| --- | --- | --- | --- | --- |
| Servo1 | PB0 | TIM3_CH3 | Servo1 | J14 Servo1 |

#### Pinout

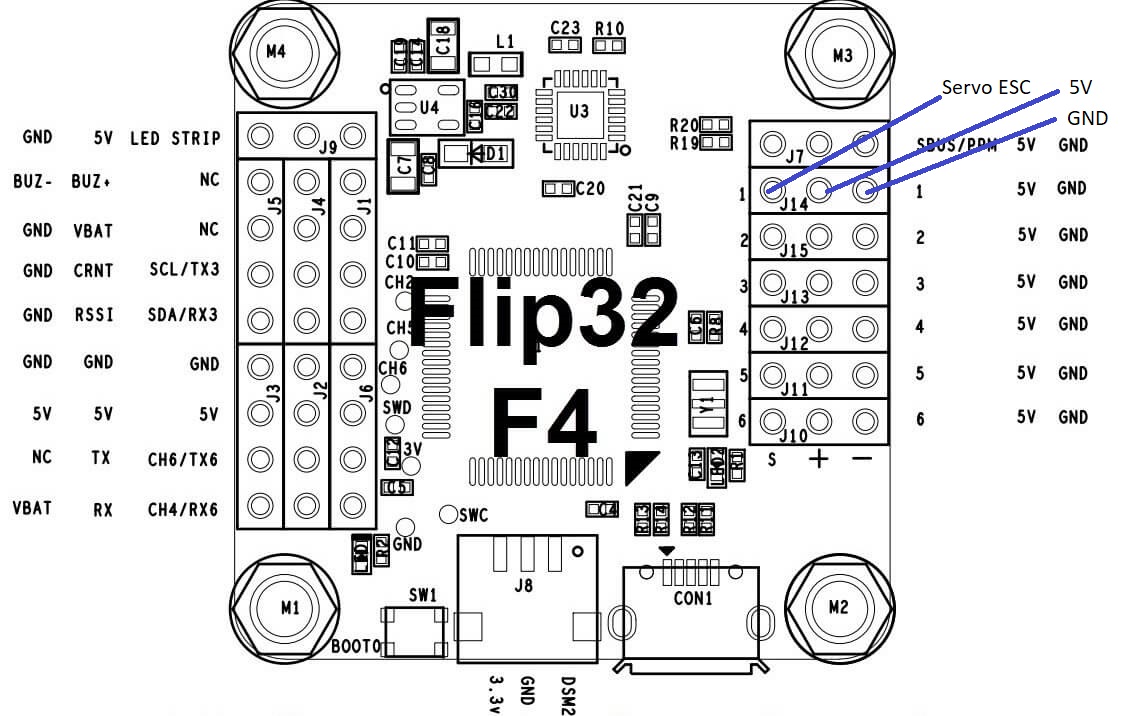
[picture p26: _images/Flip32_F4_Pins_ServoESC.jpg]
ESC Pins


In most cases the ESC will be used to power the entire CC3D Revo board and therefore the ESCs +6V signal will be connected. The CC3D Revo has power converters and protection circuits, hence the higher voltge is no problem and powering the board from USB and the ESC at the same time is supported as well.

## Associated commands

| Command | Allowed values | Description |
| --- | --- | --- |
| \$N | | print the ESC (neutral) values |
| \$N \<neutral\> \<neutral range\> \<deflection\> | | set the ESC (neutral) values, should match the ESC settings |
| \$g | | print max position error |
| \$g \<decimal\> | \>0.0;<br />100.0 will be a good value | set the max position error |
| \$i | | shows at the bottom the generated Servo1 output signal |

## Setup

The Servo1 does always generate an output signal based on the desired speed. However, as the input does use a different value range than the output, it needs to be configured separately using the \$N command.

The ESC might have a setting like this:

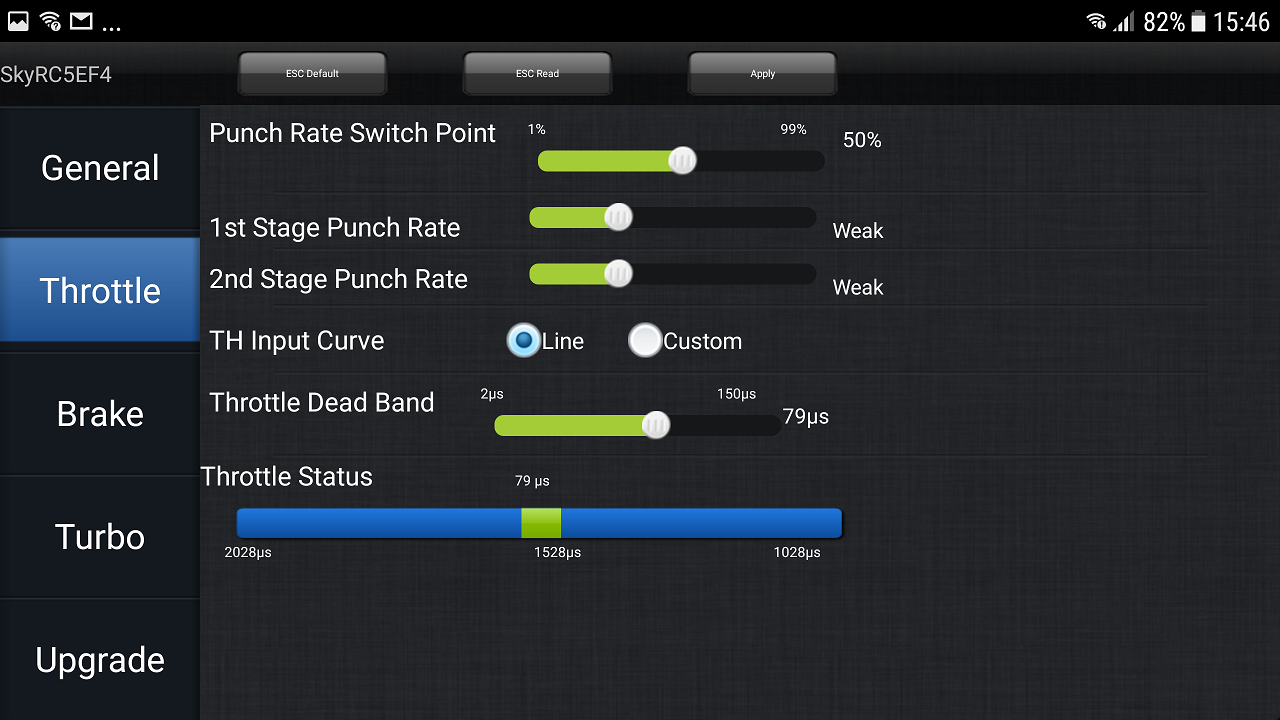
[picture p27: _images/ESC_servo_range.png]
Servo Ranges


The Throttle Status shows that values from 1028us to 2028us are allowed and a range of 79us around the midpoint of 1528us is considered Neutral. 

These settings have to match the \$N settings, so should be for this example: \$N 1528 39 461.

| \$N parameters | Values |
| --- | --- |
| Neutral point  | 1528us |
| Neutral range  | 79us/2 = 39us |
| Deflection | 2028-39-1528=461us<br />1528-39-1028=461us |

Using the \$i command the current values for input and below that, the ESC output are printed. Executng this command while holding the stick at full forward or full reverse can be used to double check the settings.

The max positional error \$g will later be needed for the end points to work with these ESCs. If the CableCam drives at speed and is configured, using the \$a setting, to brake from this speed to a full stop in 10 seconds in order to reach the end point perfectly, what creates that brake signal? The servo1 output will ask the ESC to reduce speed gradually, say 100%, 90%, 80%,....0% in those 10 seconds. Therefore only the drag brake of the ESC is used and it will likely not be strong enough. The ESC would apply a stronger brake force when the servo1 signal is neutral. But that will be too strong and for sure does not correlate with the current (de)acceleration settings. The solution is the \$g value.

The current speed is measured by the position sensor and based on that, the brake distance is calculated. Assuming the brake distance is greater than the distance to the end point, the controller does reduce the speed output, say to 90% throttle. The ESC will use the drag brake to slow down the cablecam a bit, say it slows it down to 95% of the speed. As this is not enough brake power, soon the calculation will show that the end point will be overshot significantly. If that value is more than \$g's positional error, then the controller does ouput a neutral signal instead. Now the ESC will brake as hard as it can until the brake distance is smaller than the \$g max positional error. At this point the controller does switch back to a normal throttle signal, which might have beed reduced to 50% throttle meanwhile.

## More details

At first sight the CableCam is like a RC car. It drives forward, backward and stops. One main difference however is that the CableCam should drive forward and backward in an symmetrical fashion. Many car ESCs do not support that. With those you can accelerate the car forward, putting the stick in neutral lets the car free wheeling and to brake it actively, the stick has to be put into reverse until it stops. And only then you can go in reverse direction, probably at reduced speed.
With the CableCam we want something else. Putting the stick forward drives the CableCam in one direction, neutral means stopping and reverse means driving in reverse direction at same speed as forward.
The drag brake level means how decisive the car brakes when the stick is in neutral while moving. A drag brake of zero would let the car continue to drive, slowed down only by resistance. A high drag brake means the ESC does use regenerative braking and removes kinetic energy from the car, thus stopping it more quickly.
The initial brake level controls if the motor should be energized a little bit when the car is at a stand still, thus locking it to the current position.
Unfortunately even the higest brake level settings are too weak for the CableCam to work in all instances. Most noticable when the CableCam should drive up and down a hill. Without an initial brake, it would start rolling downhill faster and faster. Thanks to the initial and drag brake it brakes but is still rolling downhill, just slower.

The best ESC would be one that supports a Closed Loop Speed control. Because then the stick position controls the speed instead of the thrust. With such an ESC a stick position of neutral would make the CableCam hold the current position, preventing it from rolling downhill at all. 
Such ESCs are quite common in industrial applications like robotics or CNC servo motors but they are also quite expensive and not meant for cars and RC implementations. So they do not have an UART input but RS232. They are quite heavy or conveniently small but support tiny motors only. Unfortunately I have not managed to convince any of the RC car ESC vendors to add a close loop mode although it would be a piece of cake for them. The hardware supports it and the logic is well known.

## Troubleshooting

One problem the CableCam controller has is, it sits between two systems and hence has to know both. The software tries to automate as much as possible but without feedback, many things are not possible. So much for the excuses. If you have ideas, please write up issues here in github.
In case you have issues, please post an [issue](https://github.com/wernerdaehn/CC3D-CableCam-Controller/issues).

* The motor does not start although everything has been configured. 

One reason the motor does not start is when the stick is not in neutral at startup. This is a safety precaution, nobody wants the CableCam or RC car to drive away at high speed right after turing it on. And this precaution is implemented in the CableCam Controller and in the ESC, both! Hence the first thing to check is the neutral point of the input. Using _$i_ the current value of the speed channel can be checked. Hence the neutral point should use this value, see the command _$n_.
With above controller allows to change the output signal from neutral do something else. Which does not help much in case this output signal for neutral is not neutral for the ESC, because then it would not allow to move the motor. The default neutral point of the ESC output is 1500, which is standard. The _$N_ command allows to change that however. The _$i_ command prints out the ESC output signal as well, which might come in handy to proof the servo signal for the ESC does change at different stick positions.

* There is a long delay when moving the stick until the motor starts

This is likely a combination of the acceleration limit and the ESC output neutral range _$N_.
To visualize this, imagine the following situation:

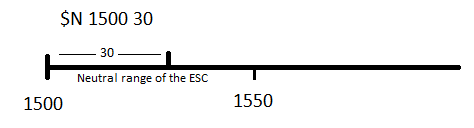
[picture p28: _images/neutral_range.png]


The neutral range of the CableCam Controller is way smaller (30us) than the range the ESC is actually using (50us). So it takes a bit until the stick is moved enough for the ESC to start moving the motor. How long depends on the amount - that will not be much - but also on the max accel setting _$a_. If it takes 1 second for the output signal to reach the +50, there is a delay of 1 second. Second, a signal of 1551 does not mean the cablecam moves. It might not be enough thrust to overcome the resistence yet. Having said that, with the configured defaults and the allowed value ranges, this should not be a huge delay.

* No slow speeds possible

Obviously the ESC itself has a minimum speed. The only reason why the cablecam controller might not be able to go equally slow is again an effect around the output neutral range _$N_. If the CableCam Controller has a larger neutral range than the ESC. Then the first output signal will be will outside the ESC's neutral range. Solution is to reduce the neutral range, e.g. _$N 1500 20 700_. Or better to the exact values as shown above.

* Forward and reverse is different

Another variation of the neutral settings, this time the neutral point is not aligned. If the center of the controller is 1500 but for the ESC it is 1520, the stick moves outside the neutral range of the ESC in one direction much faster and slower in the other.
Solution is to align the neutral point. The probably best way for that is to calibrate the ESC. You would put the controller in passtrough mode _$p 1_ and therefor the input signal is sent to the output unfiltered. No end point, no speed or accel limit is used. Now perform the ESC calibration. In case of the TS120/160 that means turning on the ESC and keeping the power button pressed until the motor does peep. Stick in neutral and press the power button on the ESC once to set the neutral point - one beep; put the stick full forward and press the button again - two beeps; put the stick in full reverse and press the button a lst time - three beeps - and the ESC is calibrated.

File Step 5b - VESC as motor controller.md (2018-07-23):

# VESC6 as Motor Controller

An ESC supporting Closed Loop speed operations is the [VESC6](http://www.trampaboards.com/vesc-6-in-cnc-t6-sealed-of-aluminum-box--vedder-electronic-speed-controller-trampa-exclusive-x1-p-23866.html). The price of 330EUR is steep though.

However the VESC6 allows much more than just controlling the speed. As it is connected via UART, the speed can be set precisely, the status of the motor controller can be read etc.

## Hardware

#### MCU Pins used

| Function | MCU Pin | MCU Function | Connector Pin | Flip32 F4  |
| --- | --- | --- | --- | --- |
| UART TX  | PA2 | USART2_TX | FlexiPort/Conn1 Pin3 | J1 SCL/TX3 |
| UART RX  | PA3 | USART2_RX | FlexiPort/Conn1 Pin4 | J1 SDA/RX3 |
| GND | | | FlexiPort/Conn1 Pin1 | J6 GND |
| 5V | | | FlexiPort/Conn1 Pin2 | J6 +5V |

#### Pinout

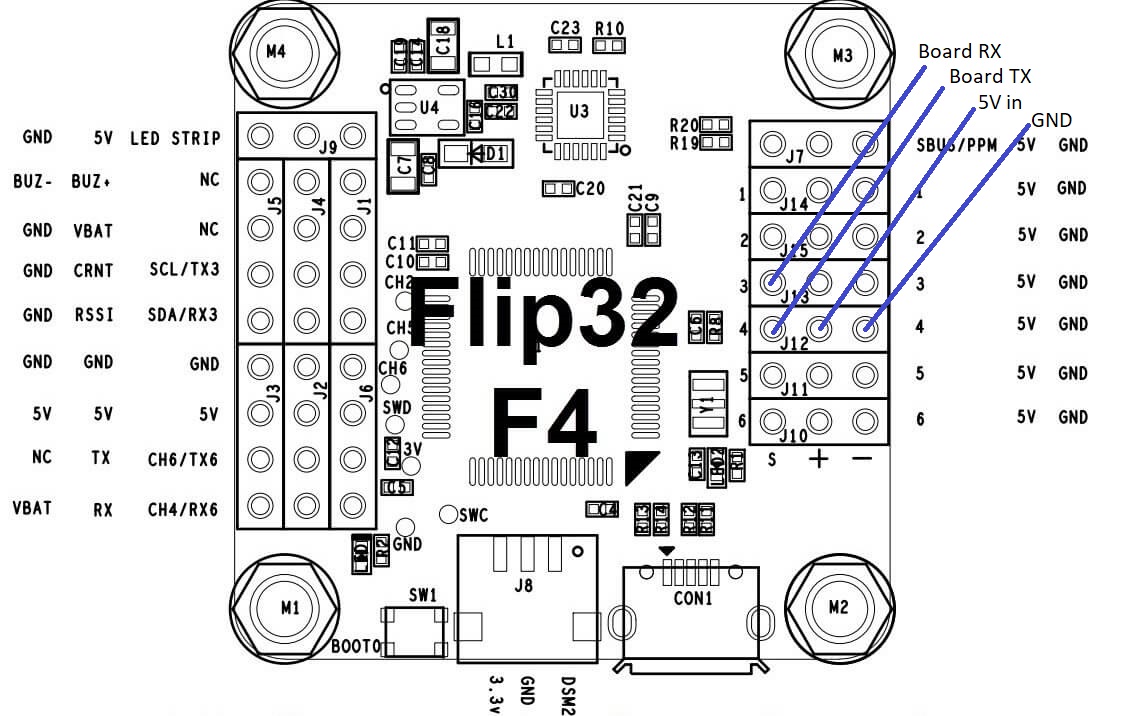
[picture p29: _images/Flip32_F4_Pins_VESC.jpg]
VESC Pins


In order to take full advantage of the VESC, the CableCam controller talks to it via UART instead of PPM signals. This allows for more fine grained control.
To connect the VESC with the CableCam Controller, Servo Out 3 is configured as UART RX - connected to VESC TX pin - and Servo Out 4 as TX - connected with VESC RX pin.
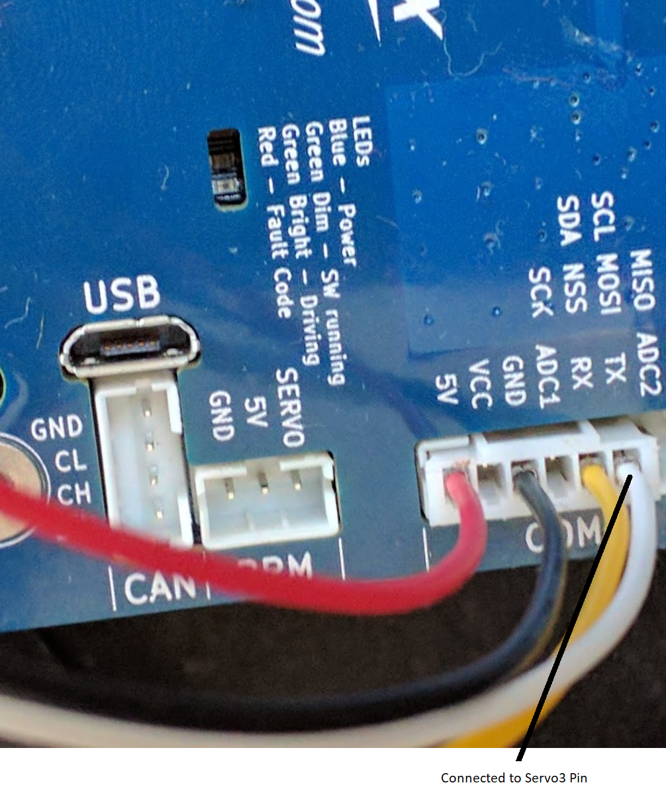
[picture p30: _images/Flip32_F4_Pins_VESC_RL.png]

As with the RC ESC, the VESC powers the CableCam Controller board via the +5V and GND of the VESC connected to one of the Servo's +5V and GND pins.

_Note: Power the CableCam Controller via +5V and **not the Vcc pin**. The latter might be a too high voltage_

## Associated commands

| Command | Allowed values | Description |
| --- | --- | --- |
| \$e | | Print the maximum eRPMs configured |
| \$e \<max erpms\> | same as the VESC6 setting (Speed Controller) | At 100% speed, the VESC will be asked to run at that speed. Hence this value should not be larger than what was configured in the VESC. |
| $E | | Print the current status of the VESC6, current speed, duty, amps, battery voltage,... |

## Setup

The VESC has to be configured to use its speed PID controller.

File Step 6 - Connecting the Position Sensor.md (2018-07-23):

# Position Sensor

To know the actual position and speed of the CableCam, on one of the running wheels a position sensor is placed. This can be anything that has two output signals and can be connected to a Quadrature Encoder.

## Hardware

#### MCU Pins used

| Function | MCU Pin | MCU Function | Connector Pin | Flip32 F4  |
| --- | --- | --- | --- | --- |
| Servo5 | PA0 | TIM5_CH1 | Servo5 | J11/Servo5 |
| Servo6 | PA1 | TIM5_CH2 | Servo6 | J4 RSSI |
| GND | | | Servo5 | Servo5 |
| Vcc | | | Servo5 | Servo5 |

Note: Yes, on the Flip32 the MCU pin PA1 is not connected to Servo6 but to RSSI!

#### Pinout

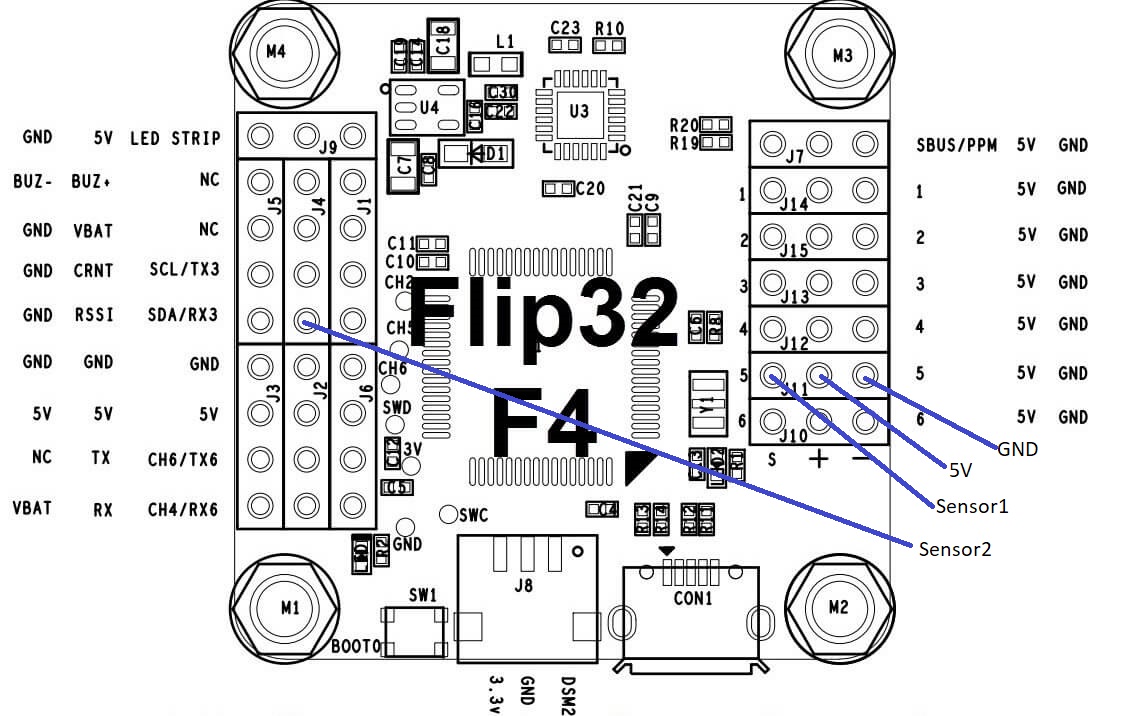
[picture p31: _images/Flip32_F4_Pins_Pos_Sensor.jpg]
UART Pins


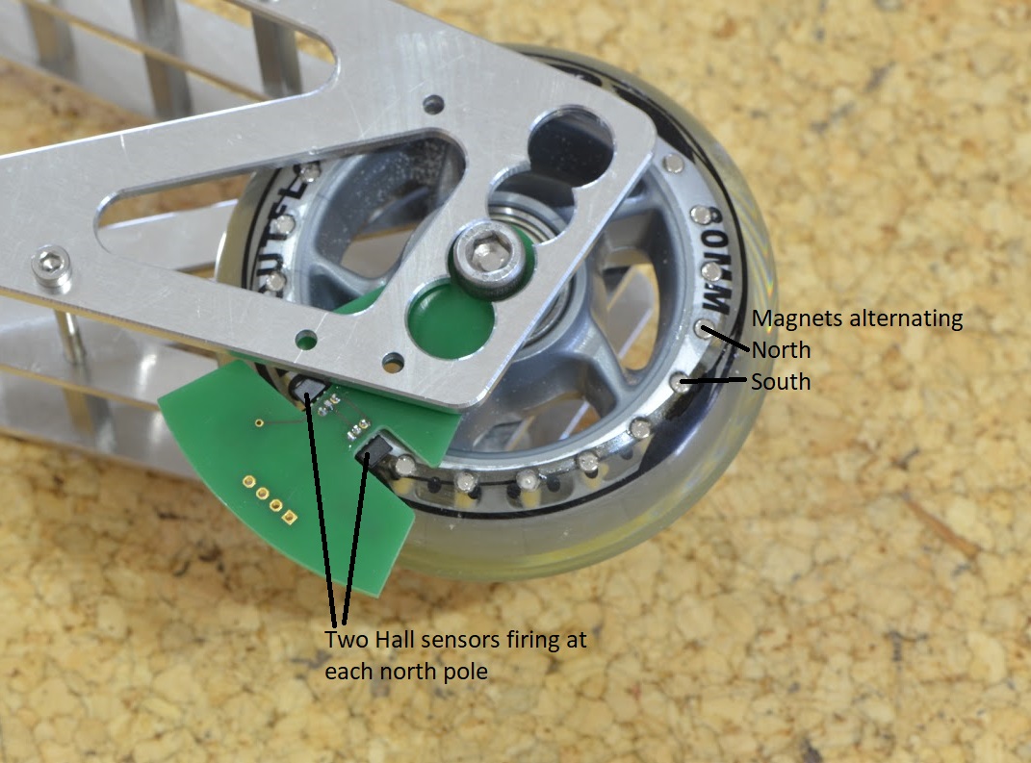
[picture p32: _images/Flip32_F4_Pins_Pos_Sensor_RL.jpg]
UART Pins


## Associated commands

| Command | Allowed values | Description |
| --- | --- | --- |
| \$p | | prints the start point, end point, current position according to the counter and current speed |

## Settings

The hall sensor is very simple. The [Allegro Microsystems A1120](http://www.allegromicro.com/en/Products/Magnetic-Digital-Position-Sensor-ICs/Hall-Effect-Unipolar-Switches/A1120-1-2-5.aspx) sensor connects the output to Gnd if the magnetic field perpenticular to the chip surface exceeds a certain level and opens that switch if it falls below a level (=Open Drain). These two levels are different, hence avoiding noise in case the magnet field is exactly at the switch level (=Hysteresis). As a result, the sensor board can be very simple. Power between 3..24V is provided - hence perfectly suited for the Vcc_unreg provided by the ESC - and a capacitor nearby the chips is needed. The output signal of both is connected directly to the Servo5&6. A pullup resistor is not needed either, the STM32 MCU internal ones are turned on for those two pins.

<a href="https://raw.githubusercontent.com/wernerdaehn/CC3D-CableCam-Controller/master/_images/Flip32_F4_Pins_Pos_Sensor_Schematic.png">
  
</a>

The only important things to make sure are

1. The hall sensor does switch on and off reliably, meaning the magnetic field has to raise above and fall below the thresholds for sure.
2. The two hall sensors have a delay between switching on/off as this delay tells the rotation direction. If both would switch on exactly the same time, no rotation direction can be derived.

To achieve that, one of the running wheels has 22 bores of d3x8mm (3mm drill and 8mm deep) and magnets are inserted alternating north/south. The hall sensor does switch on north magnetic fields only and therefore by adding a south orientated magnet between, it is an absolute certainty, the north field strength falls below the required level. 
In my case the bores are drilled into the skate wheel with a diameter of 60mm, hence the distance between each drill is 8.6mm. So as long as the distance between the two hall sensors is not 17.2mm or multiples thereof, they will not switch on/off at the same time. I aimed for a distance of 8.6mm+50% = 13mm roughly.

_Note: The sensor board PCB is currently redesigned using above guidelines. Maybe LEDs will be added as well as visual indication?_

To test if all is working, the sensor board needs to be powered and then moving the wheel should change the third output value of the \$p command, the current position.

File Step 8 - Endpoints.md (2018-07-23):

# Endpoints

Using the programming switch the CableCam can be brought into a mode where the endpoints are set. Driving the CableCam to the startpoint and tipping the end point switch makes the current position the start point limit. Then driving forward or reverse to the end point and tipping the end point switch a second time sets this as the second limit. 
When the programming switch on the TX is put back into the operational state, the CableCam can be driven only within those two points (if mode is endpoint with limiters).

To change the end points, the programming mode is entered again and the CableCam allows driving to any position, even outside of the previous set range. The sequence is always the same, first click after entering the programming mode sets the first point, all subsequent clicks modify the second end point.

Using the CableCam Controller (https://youtu.be/ohzvkKzsO8Q "Using the CableCam Controller")

The logic for the end point limiter is a bit tricky. 
Based on the stick position and the acceleration limit, the time to zero is calculated. For example, if the stick is at position +100% and the acceleration is 0.2, it takes 5 seconds to stop (=1.00 * 1/0.2). At a stick position of 50% half the time (=0.5 * 1/0.2). 

From the hall sensor the controller knows the current speed, the time to stop from the stick level, hence the distance to stop can be calculated: s = v * t / 2 [(velocity-time graph)](http://www.bbc.co.uk/education/guides/z3bqtfr/revision/5). Example: s = 200steps/s * 10s / 2 = 1000steps. (One step is one increment on the position sensor)

This calculation is made in absolute numbers and the endpoint to be considered depends on the stick direction. Moving away from an endpoint is okay, it should limit moving into an endpoint.

If the brake distance in relationship to the current positions shows that the end point will be overshot, the controller starts to reduce the speed output.

There are two failsafes implemented in addition:

1. If the calculation shows the end point will be overshot by more than \$g steps, then it does engage an emergency brake. It outputs a speed signal of neutral. This causes the ESC to brake as hard as it can.
2. Once the end point is overshot the output signal is put into neutral as well to force a stop as quickly as possible.

Both failsafes have positive and negative effects.

In a perfect world, the speed signal is reduced linear and the CableCam stops exactly at the end point. In reality however the inertia, latency and how good the ESC can be controlled put physical limits.

Above works well if the ESC supports Closed Loop operations and the acceleration is set to a value the ESC can handle easily. The speed signal is constantly lowered, a fraction of a second later the ESC does achieve the desired speed and the end point will be overshot with very little excess speed and stop. Little excess speed hopefully, else it stops abrupt at this point.

On the other hand, if the acceleration setting is "stop from 100km/h to zero in one second", this will likely not work. That would be a deceleration of 2g. Therefore it is important to set the values to something that is realistic. Given the capabilities of the ESCs, the accelerations and decelerations are much higher than even sports cars can achieve. A deceleration of 1g is no problem. But this does not provide nice and smooth shots.

On the negative side, as soon as the emergency brake kicks is, there is a significant change in brake force. For closed loop ESCs the emergency brake should never engage, hence increasing \$g from 100 to something higher might make sense. For all other ESCs the emergency brake is part of the normal brake process and a value of 100 worked out well.

## Associated commands

| Command | Allowed values | Description |
| --- | --- | --- |
| \$r | | Print the ESC motor direction |
| \$r \<direction\> | 1, 0, -1 | Set the ESC motor direction. Does the pos sensor report larger values when the RC speed signal increase? Then +1. |
| \$g | | Print the max allowed positional error before the emergency brake kicks in |
| \$g \<steps\> | \>0 | Set the max allowed position error |

## Setup

For the endpoints to work properly, the \$r setting is important. Once an endpoint has been overshot, moving the CableCam back into the safe area is allowed, driving deeper into the forbidden area is not. Therefore it is important for the controller to know what the receiver input means for the ESC, driving into the one or the other direction.

To simplify the setup, the default is \$r 0 meaning the controller should watch the cablecam during the end point setting and set \$r itself. It does that by calculating the integral of all speed signals starting with the first position. If the end position is higher than the start position and the ESC signal was positive, then \$r 1 is set. A stick >0% means increasing the position. Hence the controller knows that at the start point a stick >0% drives the CableCam back into the safe zone, at the end point a value <0% drives it back into the safe zone.

Might be a good idea to save that setting afterwards.

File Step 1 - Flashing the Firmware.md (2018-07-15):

# Flashing the Firmware

_Note: All drivers used are included in a standard Windows 10 installation._
1. Install the ST provided DfuSe utility from the bottom of [this page](http://www.st.com/en/development-tools/stsw-stm32080.html).
1. Run the installed DfuSe program.
1. Connect the board to your computer via USB and while doing so, keep the _boot_ button pressed. When the board is powered with the boot button pressed, the STM32 internal USB bootloader is started instead of the firmware.
1. As this activates the STM32F4 hardware bootloader and no firmware runs, only the Power LED should be on. If the Status LED does blink, the firmware is active. Try again above step.
1. Download the firmware from this project https://github.com/wernerdaehn/CC3D-CableCam-Controller/blob/master/bin/Debug/CableCamControllerF4.dfu
1. At the bottom of the utility, in the _Upgrade or Verify Action_ area, click on _Choose_ and select above's downloaded CableCamControllerF4.dfu file. 

1. The DfuSe Utility should show in the top box the text _STM Device in DFU Mode_. This indicates the board's hardware bootloader is running. 
1. If it does, the _Upgrade_ button copies the firmware onto the board. 

1. The next dialog(s) is to be confirmed with _yes_. We are certain the firmware is for the STM32F405RG chip.
1. To validate the flashing was successful, the _Verify_ action should be triggered, just to doublecheck.
1. At the top is the _Leave DFU mode_ button to restart the controller with the new firmware.
1. A first indication that everything is normal is when the Status LED on the board does flash with 1Hz.

Just to clarify. This is a new firmware. All the previous installed code is removed by that procedure from the board, no software bootloader, no previous firmware. So connecting this board to CC3D Revo software like the Ground Station will no longer work. You would need above method to reinstall the software bootloader of OpenPilot.

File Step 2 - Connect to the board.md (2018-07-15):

# Connecting to the Controller

The CableCam Controller firmware was uploaded and either in the DFUSe tool the _Leave DFU Mode_ button was pressed or the board was connected without the boot button being pressed. 

1. As the board is connected to the computer via USB, a new COM port is available to interact with the CableCam Controller.
1. This can be validated by starting the Windows 10 Device Manager, it should have a new com port called _STMicroelectronics Virtual COM Port or _USB Serial Port_. The port name in brackets, here _COM3_ is the one to use in the terminal. 
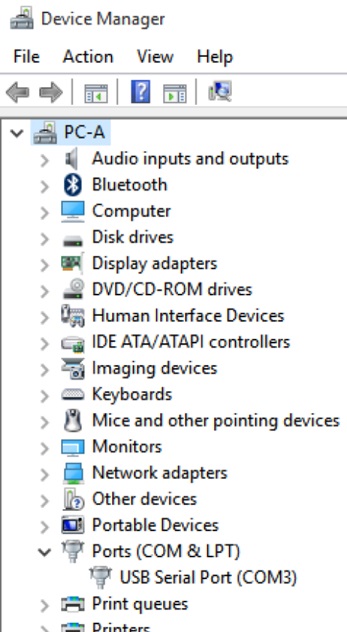
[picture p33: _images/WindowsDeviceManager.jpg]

1. Open a serial terminal in order to talk to the board. The one I use is [putty](https://www.chiark.greenend.org.uk/~sgtatham/putty/latest.html) as 64Bit install or just the 64Bit exe download.
1. In the terminal create a new serial connection to the port shown in the device manager. In putty that means clicking on _serial_ and entering the above portname like _COM3_. The settings for baud rate etc are irrelevant and can be left at their defaults.
1. To test if everything works properly, a first command can be sent by typing _$h_ for help and confirming the command with the return key.
1. This should print status information plus a help text in the console.
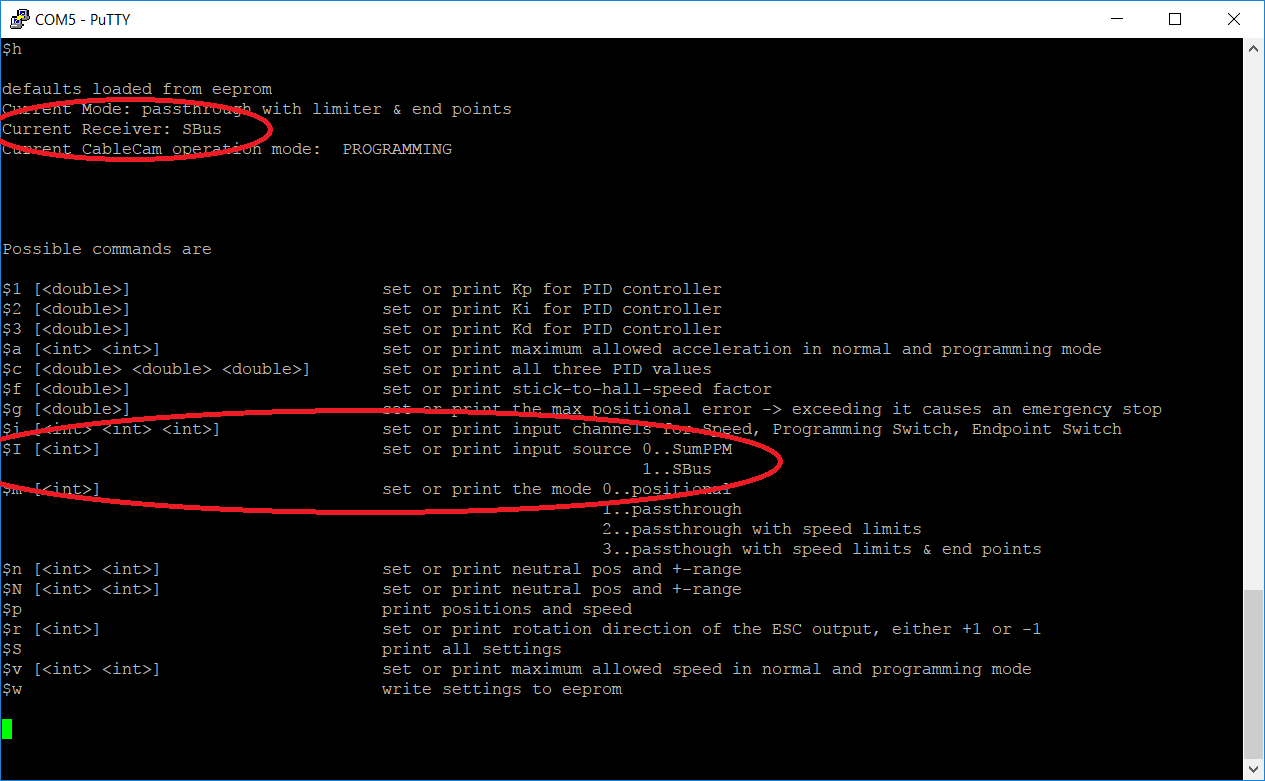
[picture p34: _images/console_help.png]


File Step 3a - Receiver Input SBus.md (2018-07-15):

# Receiver input - SBus

The CableCam Controller is put between the RC receiver and the motor controller (ESC). The controller acts as a filter of the input provided by the receiver and the output sent to the motor controller.

One supported receiver type is SBus commonly used with Futaba and FrSky.

## Hardware

#### MCU Pins used

| Function | MCU Pin | MCU Function | Connector Pin | Flip32 F4 |
| --- | --- | --- | --- | --- |
| UART3 RX | PA10 | USART1_RX | MainUSART Pin 4 | SBUS/PPM/J7 |

#### Pinout

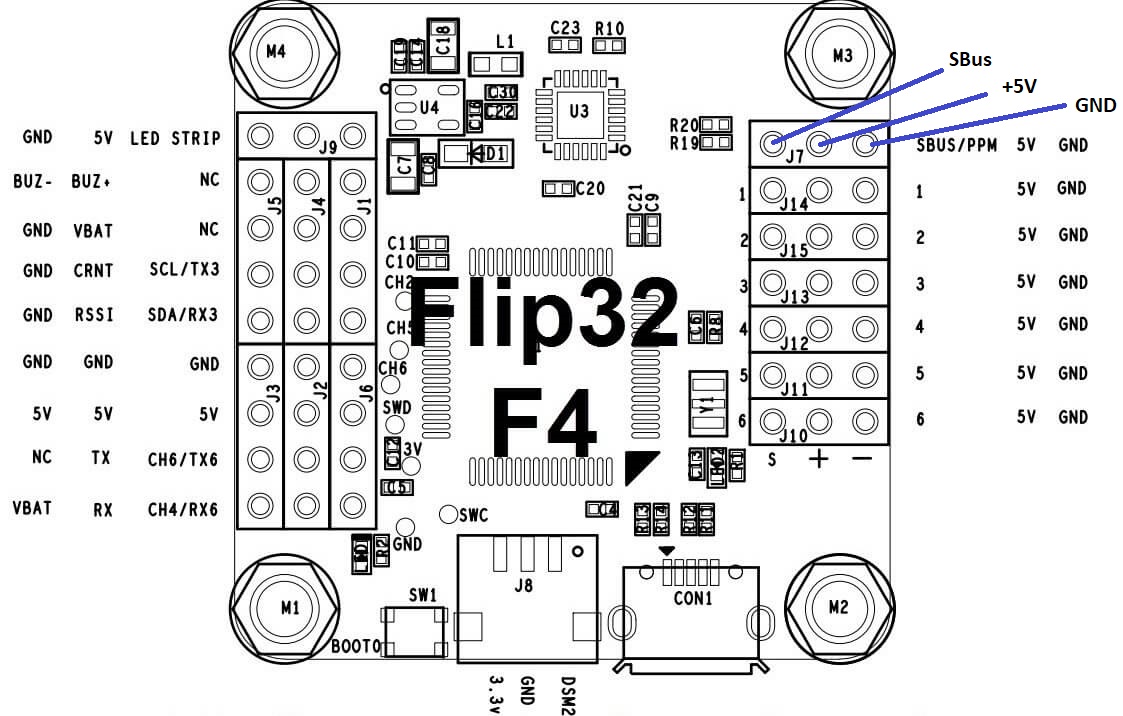
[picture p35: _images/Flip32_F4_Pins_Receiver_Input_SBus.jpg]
UART Pins


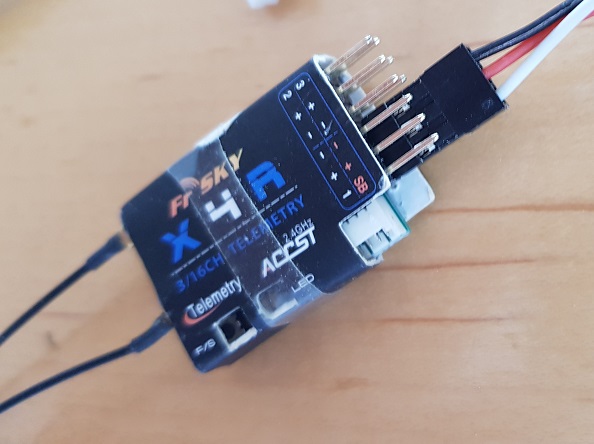
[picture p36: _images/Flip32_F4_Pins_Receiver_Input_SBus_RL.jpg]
UART Pins


## Associated commands

| Command | Allowed values | Description |
| --- | --- | --- |
| \$I | | Print the current input |
| \$I 1 | 1 | Set the input to SBus |
| \$d s | | print the last SBus packet and some statistics for debugging |
| \$i | | print the current values received from the SBus |

## Settings

The first step is to tell the controller which function to use for decoding the receiver input signal, SBus or SumPPM. With \$I 1 it is set to SBus mode and if the receiver is connected and powered (all three pins, SBus, +5V and GND are connected) and the receiver getting values from the RC sender, the CableCam Controller should start to receive valid inputs immediately. To proof that, \$i can be used to print the current input.

This screen shows when the last input was received and the values for each channel. Correct values are something between 200 and 2000.

If the values are all zero, the following checks should be made

- Is the sender linked with the receiver at the moment? The receiver does not output anything as long as it did not receive anything from the RC sender.
- Is the receiver powered?
- Does the \$I command return 1?
- Is the hardware connection correct, receiver to controller?

In case nothing can be found, the debug command \$d s prints out everything about the serial input line, e.g. if packets have been received at all, noise errors,... and the last buffer content. If all is zero, no byte has ever been received.

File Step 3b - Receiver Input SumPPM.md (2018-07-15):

# Receiver input - SumPPM

The CableCam Controller is put between the RC receiver and the motor controller (ESC). The controller acts as a filter of the input provided by the receiver and the output sent to the motor controller.

One supported receiver type is SumPPM commonly found with Graupner receivers and many others.

## Hardware

#### MCU Pins used

| Function | MCU Pin | MCU Function | Connector Pin | Flip32 F4 |
| --- | --- | --- | --- | --- |
| UART3 RX | PA10 | USART1_RX | MainUSART Pin 4 | SBUS/PPM/J7 |

#### Pinout

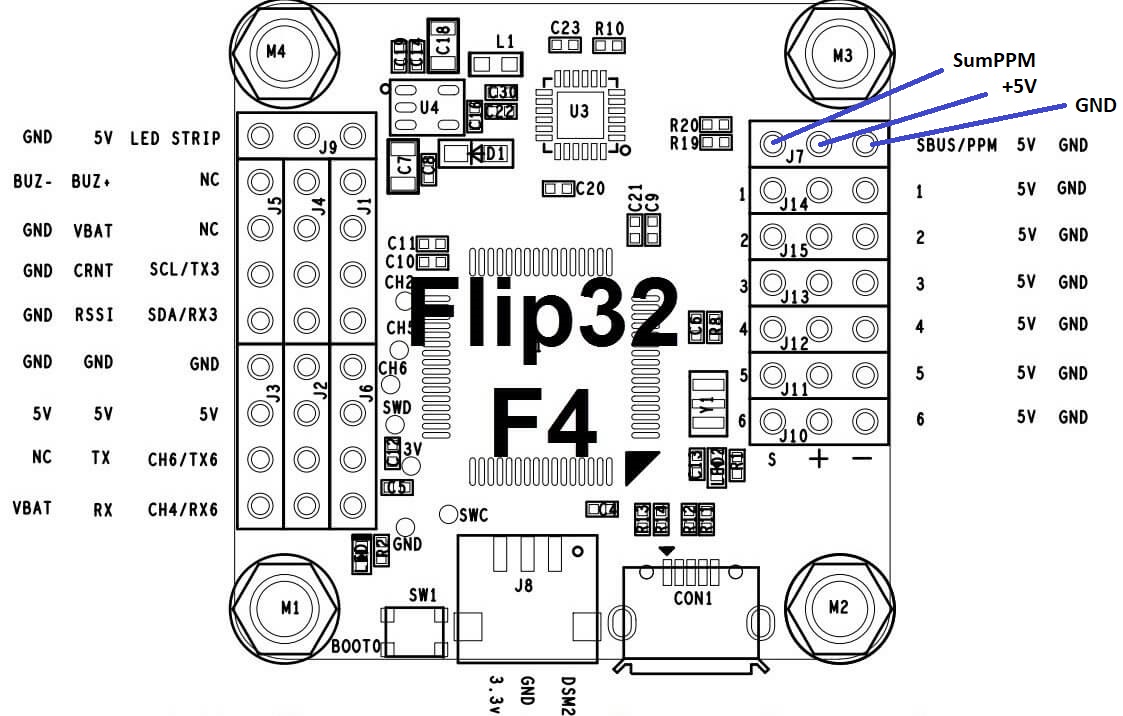
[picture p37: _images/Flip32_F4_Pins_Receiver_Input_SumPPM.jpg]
UART Pins


## Associated commands

| Command | Allowed values | Description |
| --- | --- | --- |
| \$I | | Print the current input |
| \$I 0 | 0 | Set the input to SumPPM |
| \$d p | | print the last SumPPM packet for debugging |
| \$i | | print the current values received |

## Settings

The first step is to tell the controller which function to use for decoding the receiver input signal, SBus or SumPPM. With \$I 0 it is set to SumPPM mode and if the receiver is connected and powered (all three pins, SBus, +5V and GND are connected) and the receiver getting values from the RC sender, the CableCam Controller should start to receive valid inputs immediately. To proof that, \$i can be used to print the current input.

This screen shows when the last input was received and the values for each channel. Correct values are something between 900 and 2100.

If the values are all zero, the following checks should be made

- Is the sender linked with the receiver at the moment? The receiver does not output anything as long as it did not receive anything from the RC sender.
- Is the receiver powered?
- Does the \$I command return 0?
- Is the hardware connection correct, receiver to controller?
- Is it really a SumPPM signal? What does \$d p show?

The debug command \$d p was added to see the current timings. The output might look like

```
Duty & Pause Timing for SumPPM:   
1123   398   1690   398   1123   398   1122   398   7879   401   1122   399   1123   398
1123   399   1123   398   1123   399   1690   398   1122   399   1123   398   7879   401
1122   399   1122   398   1123   399   1123   398   1123   399   1690   399   1122   399
1123   399   7880   401   1123   399   1123   399   1123   398   1124   399   1123   398
1691   399   1123   398   1123   399   7879   401 
```

This shows the time between falling and raising flanks (both). A SumPPM signal consist of a long high phase, indicating the packet end. So reformatting the data with the long pause as last entry proofs this is a valid signal.

Duty & Pause Timing for SumPPM:   
1123   398   1690   398   1123   398   1122   398   **7879**   401
1122   399   1123   398   1123   399   1123   398   1123   399   1690   398   1122   399   1123   398   **7879**   401
1122   399   1122   398   1123   399   1123   398   1123   399   1690   399   1122   399   1123   399   **7880**   401
1123   399   1123   399   1123   398   1124   399   1123   398   1691   399   1123   398   1123   399   **7879**   401 

A SumPPM signal with 8 channels.

Another example could look like:

```
Duty & Pause Timing for SumPPM:   1097   18879   1098   18880   1097   18881   1098   18880...
```

This is clearly a regular servo (single channel) only. It is a puls width of 1097 followed by a looong pause. The receiver does not output a SumPPM signal obviously.

A normal \$i output would look like this:

UART Pins

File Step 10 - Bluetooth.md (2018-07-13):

# Bluetooth/UART control

The controller supports getting commands via UART as well, usually connected to a bluetooth receiver like the HC-06. With that it is possible to change settings via an app, monitor the status via a serial bluetooth terminal, change settings on the spot.

## Hardware

#### MCU Pins used

| Function | MCU Pin | MCU Function | Connector Pin | Flip32 F4  |
| --- | --- | --- | --- | --- |
| UART TX  | PB10 | USART3_TX | FlexiPort/Conn1 Pin3 | J1 SCL/TX3 |
| UART RX  | PB11 | USART3_RX | FlexiPort/Conn1 Pin4 | J1 SDA/RX3 |
| GND | | | FlexiPort/Conn1 Pin1 | J6 GND |
| Vcc | | | FlexiPort/Conn1 Pin2 | J6 +5V |

#### Pinout

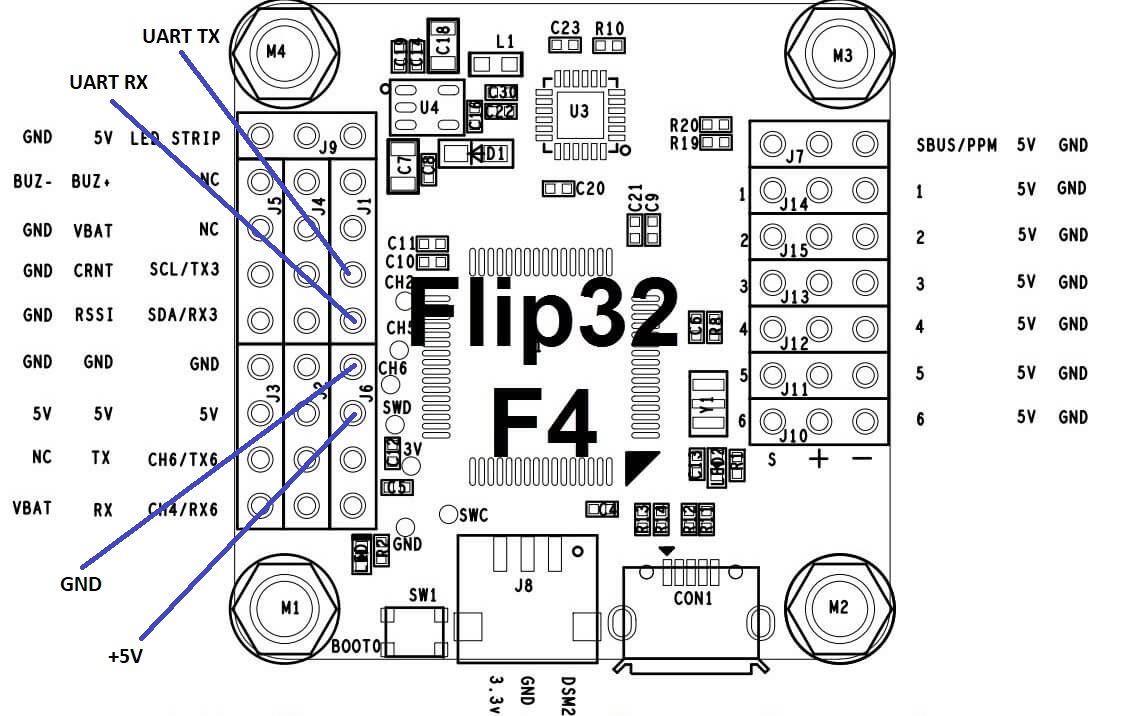
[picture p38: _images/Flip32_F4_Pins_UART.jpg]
UART Pins


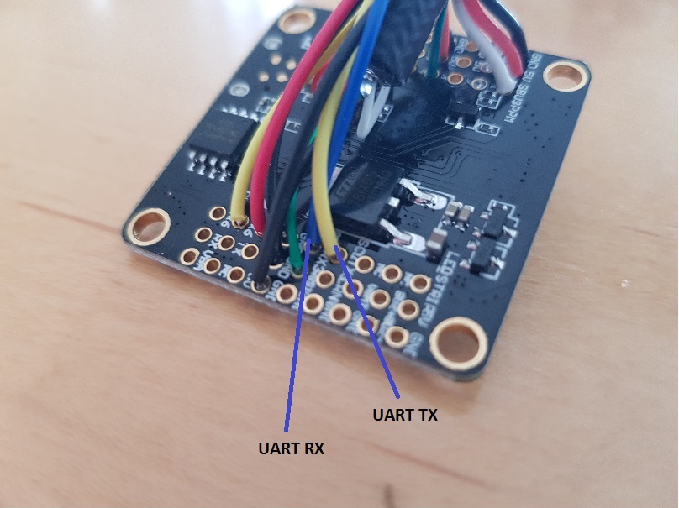
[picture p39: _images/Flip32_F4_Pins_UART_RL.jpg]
UART Pins


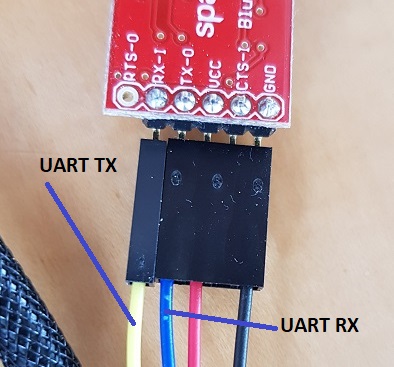
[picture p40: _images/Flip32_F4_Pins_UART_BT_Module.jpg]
UART Pins


## Associated commands

| Command | Allowed values | Description |
| --- | --- | --- |
| \$B | | Run the HC-06 configuration wizard. Works with HC-06 bluetooth modules only. |

## Settings

The UART port is configured for 38400 8n1 and the bluetooth module needs to match that setting. How to change the settings is dependent on the bluetooth module being used.

The shown [Sparkfun Bluetooth Mate Gold](https://www.sparkfun.com/products/12580) is very convenient, it allows configuration of the UART port via the connected bluetooth device.

The more populare HC-06 module can be configured by AT commands. The HC-05 has an additional KEY Pin that needs to be dealt with. Details can be found in many places, e.g. [here](http://www.instructables.com/id/AT-command-mode-of-HC-05-Bluetooth-module/). As the HC-06 is so popular, the CableCam Controller has a command \$B that does configure it automatically via the USB terminal. Connect it to the board, make sure your tablet/computer is not connected with the HC-06 at the moment, because then it accepts AT commands from the UART side. The \$B command sends AT commands at various baud rates and when it gets a valid response, it executes the commands to make some changes. The command outputs the details about what it does.

On the tablet an app proven to work well is the [Serial Bluetooth Terminal](https://play.google.com/store/apps/details?id=de.kai_morich.serial_bluetooth_terminal).

## Which Bluetooth Module to use?

The majority of the bluetooth modules are Class 2 with a range of up to 10m. Not much for a cablecam. The [Sparkfun Mate Gold](https://www.sparkfun.com/products/12580) is one of the few Class 1 devices and has a supposed range of 100m.

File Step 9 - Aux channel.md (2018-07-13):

# AUX channel

The controller supports an AUX servo output. If an input channel is mapped to the AUX function, then the RC sender can control this function. The idea for that was primarily for a braking servo. At speed near zero a button is flipped and then a mechanical brake would be engaged. 

But actually, this AUX channel can be used for many things, control a camera focus motor,...

## Hardware

#### MCU Pins used

| Function | MCU Pin | MCU Function | Connector Pin | Flip32 F4  |
| --- | --- | --- | --- | --- |
| Servo 2  | PB1 | TIM3_CH4 | Servo2 | Servo2/J15 |

#### Pinout

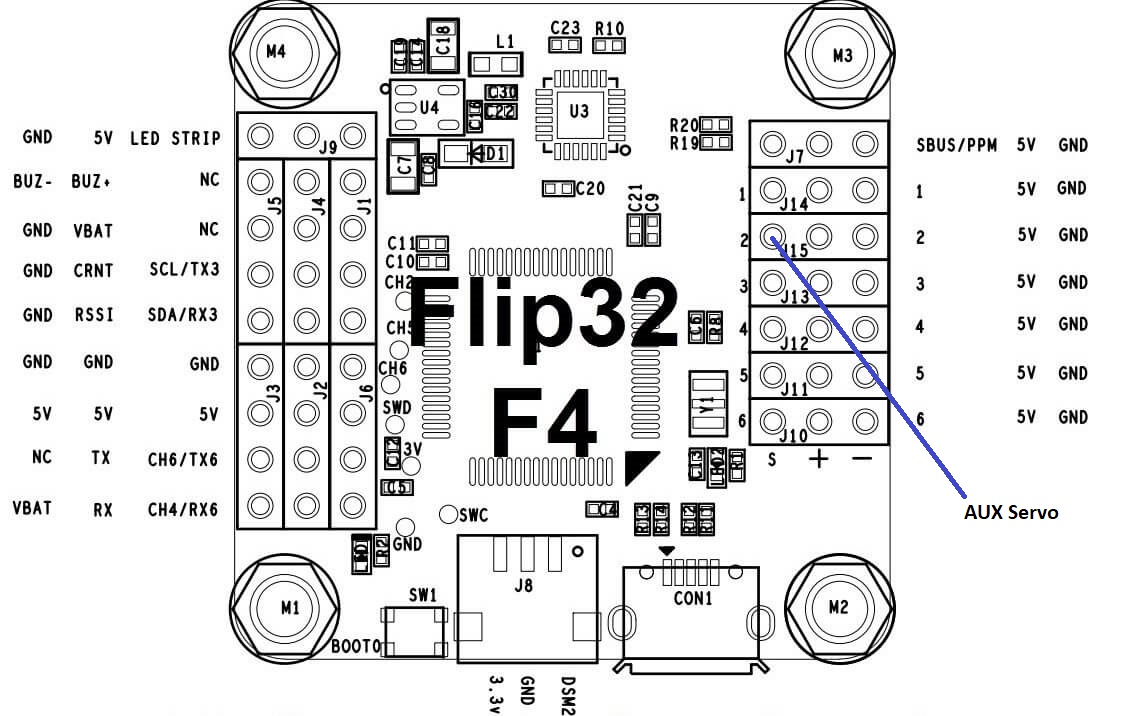
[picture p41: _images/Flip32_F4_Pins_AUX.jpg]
UART Pins


## Associated commands

| Command | Allowed values | Description |
| --- | --- | --- |
| \$j a | | Print the current mapping |
| \$j a \<channel #\> | 1...16 or 256 to unmap | Set the channel for AUX |
| \$A | | print the current AUX output timings |
| \$A \<neutral\> \<neutral range\> \<max deflection\> | integers of microseconds | Set the AUX output timings |

## Settings

First step is to assign an input channel to this function: \$j a \<channel #\>

For example \$j a 14 would set the channel #14 of the RC sender to be used as input. If this channel is at neutral, the AUX output would be neutral, putting it to max would output the max allowed puls width for the servo.

Because this AUX channel might have a different neutral range, this can be configured by the command \$A. For example \$A 1500 5 695 would set the neutral point to 1500, the neutral range to 5 and allow a max deflection of 695. In other words, neutral is 1500us, max is 1500+5+695=2200us, min is 1500-5-695=800us puls lengths.

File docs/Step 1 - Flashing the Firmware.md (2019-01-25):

# Flashing the Firmware

_Note: All drivers used are included in a standard Windows 10 installation._
1. Install the ST provided DfuSe utility from the bottom of [this page](http://www.st.com/en/development-tools/stsw-stm32080.html).
1. Run the installed DfuSe program.
1. Connect the board to your computer via USB and while doing so, keep the _boot_ button pressed. When the board is powered with the boot button pressed, the STM32 internal USB bootloader is started instead of the firmware.
1. As this activates the STM32F4 hardware bootloader and no firmware runs, only the Power LED should be on. If the Status LED does blink, the firmware is active. Try again above step.
1. Download the firmware from this project https://github.com/wernerdaehn/CC3D-CableCam-Controller/blob/master/bin/Debug/CableCamControllerF4.dfu
1. At the bottom of the utility, in the _Upgrade or Verify Action_ area, click on _Choose_ and select above's downloaded CableCamControllerF4.dfu file. 

1. The DfuSe Utility should show in the top box the text _STM Device in DFU Mode_. This indicates the board's hardware bootloader is running. 
1. If it does, the _Upgrade_ button copies the firmware onto the board. 

1. The next dialog(s) is to be confirmed with _yes_. We are certain the firmware is for the STM32F405RG chip.
1. To validate the flashing was successful, the _Verify_ action should be triggered, just to doublecheck.
1. At the top is the _Leave DFU mode_ button to restart the controller with the new firmware.
1. A first indication that everything is normal is when the Status LED on the board does flash with 1Hz.

Just to clarify. This is a new firmware. All the previous installed code is removed by that procedure from the board, no software bootloader, no previous firmware. So connecting this board to CC3D Revo software like the Ground Station will no longer work. You would need above method to reinstall the software bootloader of OpenPilot.

## Updating the firmware

Once the firmware is installed, there is a second way to bring the controller into the DFU mode, other than pressing the boot button while powering up the device: the \$_ command. 

This command disables the USB communication and then reboots the device in DFU mode.

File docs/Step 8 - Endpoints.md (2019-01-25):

# Endpoints

Using the programming switch the CableCam can be brought into a mode where the endpoints are set. Driving the CableCam to the startpoint and tipping the end point switch makes the current position the start point limit. Then driving forward or reverse to the end point and tipping the end point switch a second time sets this as the second limit. 
When the programming switch on the TX is put back into the operational state, the CableCam can be driven only within those two points (if mode is endpoint with limiters).

To change the end points, the programming mode is entered again and the CableCam allows driving to any position, even outside of the previous set range. The sequence is always the same, first click after entering the programming mode sets the first point, all subsequent clicks modify the second end point.

Using the CableCam Controller (https://youtu.be/ohzvkKzsO8Q "Using the CableCam Controller")

The logic for the end point limiter is a bit tricky. 
Based on the stick position and the acceleration limit, the time to zero is calculated. For example, if the stick is at position +100% and the acceleration is 0.2, it takes 5 seconds to stop (=1.00 * 1/0.2). At a stick position of 50% half the time (=0.5 * 1/0.2). 

From the position sensor the controller knows the current speed, the time to stop from the stick level, hence the distance to stop can be calculated: s = v * t / 2 [(velocity-time graph)](http://www.bbc.co.uk/education/guides/z3bqtfr/revision/5). Example: s = 200steps/s * 10s / 2 = 1000steps. (One step is one increment of the position sensor)

This calculation is made in absolute numbers and the endpoint to be considered depends on the stick direction. Moving away from an endpoint is okay, it should limit moving into an endpoint.

If the brake distance in relationship to the current positions shows that the end point will be overshot, the controller starts to reduce the speed output.

There are two failsafes implemented in addition:

1. If the calculation shows the end point will be overshot by more than \$g percent, then it does engage an emergency brake. It outputs a speed signal of neutral. This causes the ESC to brake as hard as it can.
2. Once the end point is overshot the output signal is put into neutral as well to force a stop as quickly as possible.

Both failsafes have positive and negative effects.

In a perfect world, the speed signal is reduced linear and the CableCam stops exactly at the end point. In reality however the inertia, latency and how good the ESC can be controlled have physical limits.

Above works well if the ESC supports Closed Loop operations and the acceleration is set to a value the ESC can handle easily. The speed signal is constantly lowered, a fraction of a second later the ESC does achieve the desired speed and the end point will be overshot with very little excess speed and stop. Little excess speed hopefully, else it stops abrupt at this point.

To allow this little excess speed to be reduced gracefully there is an offset (\$o) value. The internal calculation tries to stop at the endpoints but moved inward by the offset. And only once the actual endpoint is overshot, the controller puts the speed to zero for an immediate stop.

On the other hand, if the acceleration setting is "stop from 100km/h to zero in one second", this will likely not work. That would be a deceleration of 2g. Therefore it is important to set the values to something that is realistic. Given the capabilities of the ESCs, the accelerations and decelerations are much higher than even sports cars can achieve. A deceleration of 1g is no problem. But this does not provide nice and smooth shots.

On the negative side, as soon as the emergency brake kicks is, there is a significant change in brake force. For closed loop ESCs the emergency brake should never engage, hence increasing \$g from 100 to something higher might make sense. For all other ESCs the emergency brake is part of the normal brake process and a value of 100 worked out well.

## Associated commands

| Command | Allowed values | Description |
| --- | --- | --- |
| \$r | | Print the ESC motor direction |
| \$r \<direction\> | 1, 0, -1 | Set the ESC motor direction. Does the pos sensor report larger values when the RC speed signal increase? Then +1. |
| \$g | | Print the max allowed positional error before the emergency brake kicks in |
| \$g \<percent\> | \>0 | Set the max allowed position error in percent of the brake distance. If the calculated brake distance is 1000 steps, \$g set to 0.1 (=10%), then the emergency brake kicks in if the distance to the endpoint is below 900 steps. |
| \$o |  | Print the end point offset |
| \$o <steps> | 0...1000 | Set the end point offset. This is the mathematical point the controller will try to stop at. The cablecam's inertia will cause to overshoot that point slightly. |

## Setup

For the endpoints to work properly, the \$r setting is important. Once an endpoint has been overshot, moving the CableCam back into the safe area is allowed, driving deeper into the forbidden area is not. Therefore it is important for the controller to know what the receiver input means for the ESC, driving into the one or the other direction.

To simplify the setup, the default is \$r 0 meaning the controller should watch the cablecam during the end point setting and set \$r itself. It does that by calculating the integral of all speed signals starting with the first position. If the end position is higher than the start position and the ESC signal was positive, then \$r 1 is set. A stick \>0% means increasing the position. Hence the controller knows that at the start point a stick \>0% drives the CableCam back into the safe zone, at the end point a value <0% drives it back into the safe zone.

Might be a good idea to save that setting afterwards.

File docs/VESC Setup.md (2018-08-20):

# VESC6 Configuration

To help with the VESC configuration, the steps tp configure it for the CableCam use - after firmware update - are described here.

## Basics about a brushless motor controller

A brushless motor is essentially maintenance free, strong and simple to use. In the industry they are found everywhere. They consist of three power connectors and by applying power to two of them, the motor's next magnet ist pulled to the powered winding. Then the next winding is powered etc.

This technique opens two questions

1. Where is the motor at the moment? Else it is unknown which winding to power.
2. How much power to apply?

There are multiple strategies for that and the more sophistication is but into those two factors, the better the motor will operate.

Two terms are important here: [FOC](https://en.wikipedia.org/wiki/Vector_control_(motor)) and Encoder.

## Setup procedure

It is assumed that the Vesc controller and the motor are connected, the motor is using Hall sensors, all is powered up, the VESC is of latest firmware and the Vesc Tool connected.

#### Step 1 - FOC values

In the FOC screen of the motor settings a few parameters need to be entered. The only setting known at this point is the sensor mode - it should use Hall Sensors. Luckily the other parameters the Vesc can measure itself. 

At the bottom is the "Detect and Calculate Parameters" sequence of buttons, which starts with a short help and pressing one button after the other triggers the various measurements. Once RL and λ are created, the last button - Apply - copies the values to the top settings. On the right hand side is a button to write these settings to the Vesc permanently.

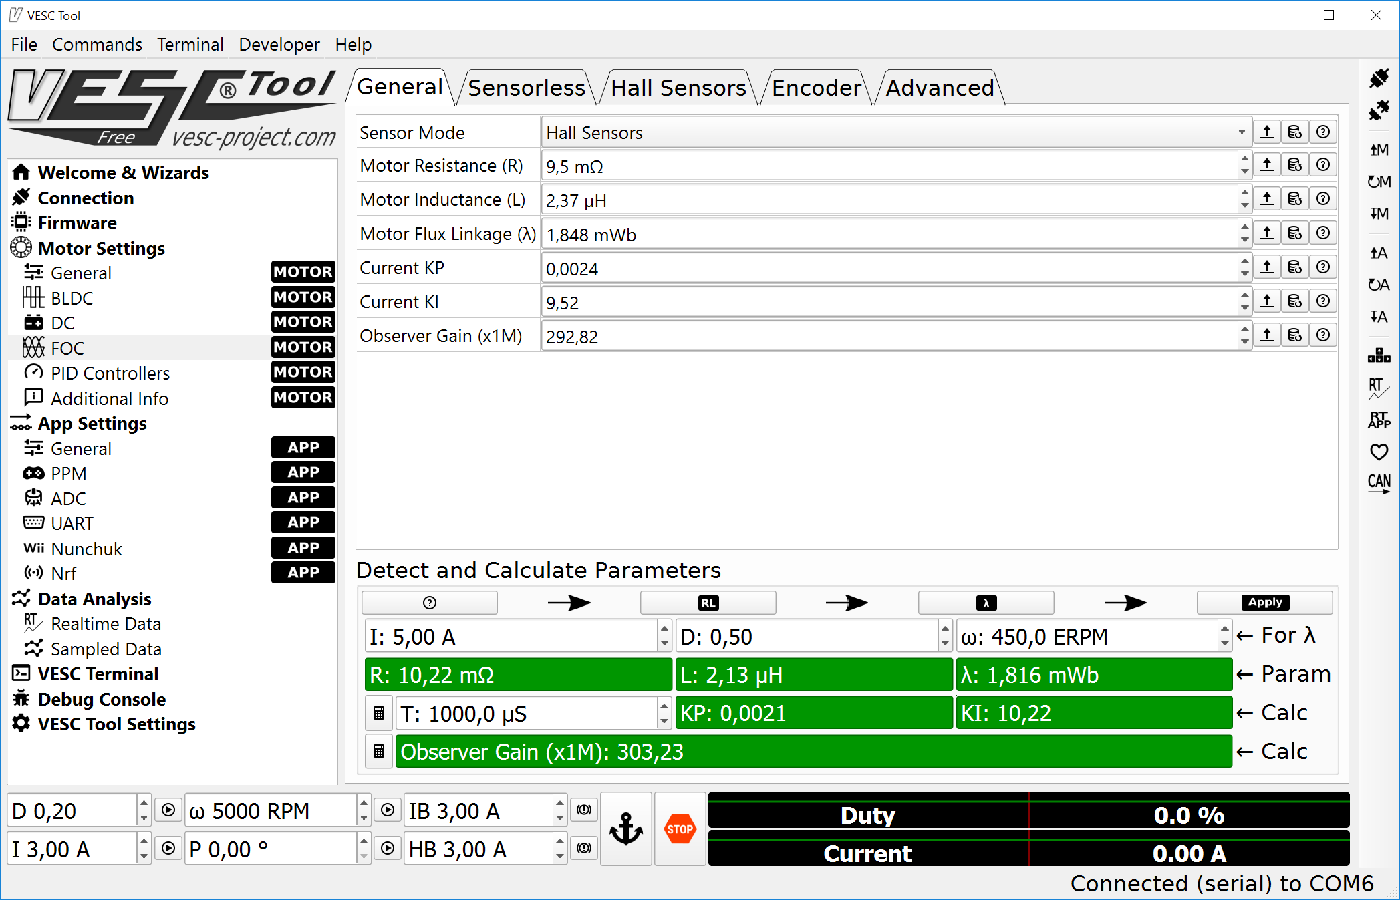
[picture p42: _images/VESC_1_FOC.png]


#### Step 2 - Hall Sensor

The three Hall sensors do switch on and off at particular angles of the motor. One full sequence has six positions and is divided into values from 0 to 200. While normal ESCs require to connect the three motor phases and the three Hall sensors in a particular order, the Vesc does rather measure the positions.

At the bottom "Detect Hall Sensors" is a Play button which turns the motor with the configured 10A power. With Apply the values are copied to the top. First and last values are irrelevant (255 always).

As this is measured the values might be different by a few percent per run which is just fine.

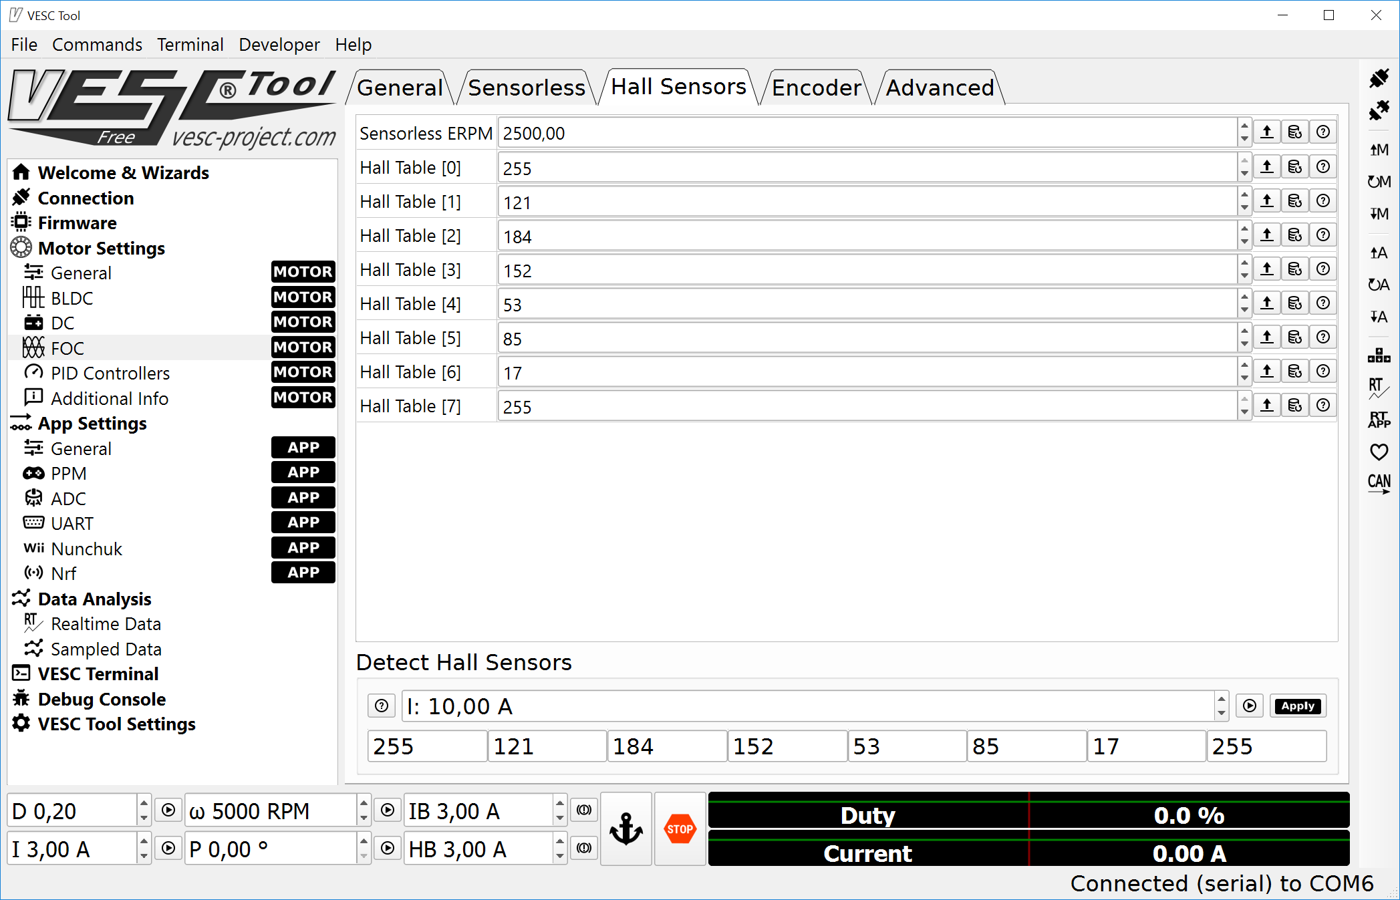
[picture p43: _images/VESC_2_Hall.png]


#### Step 3 - PID control loop

The main advantage of the Vesc is its speed controller, also called Closed Loop. A target rpm value is sent to the Vesc and it will do whatever is necessary to get to this speed and keep it. Driving uphill, rolling downhill and braking,.... the Speed Controller logic takes care of that.

Setting the right values can be quite difficult but the defaults should be good enough. At the very bottom left is a "ω 5000 RPM" and its Play button. This allows to test the speed controller.

Two values are important here however. First is the Minimum ERPM" as at the current implementation does not work for low speeds. Every RPM command below this threshold stops the motor. And to allow active braking.

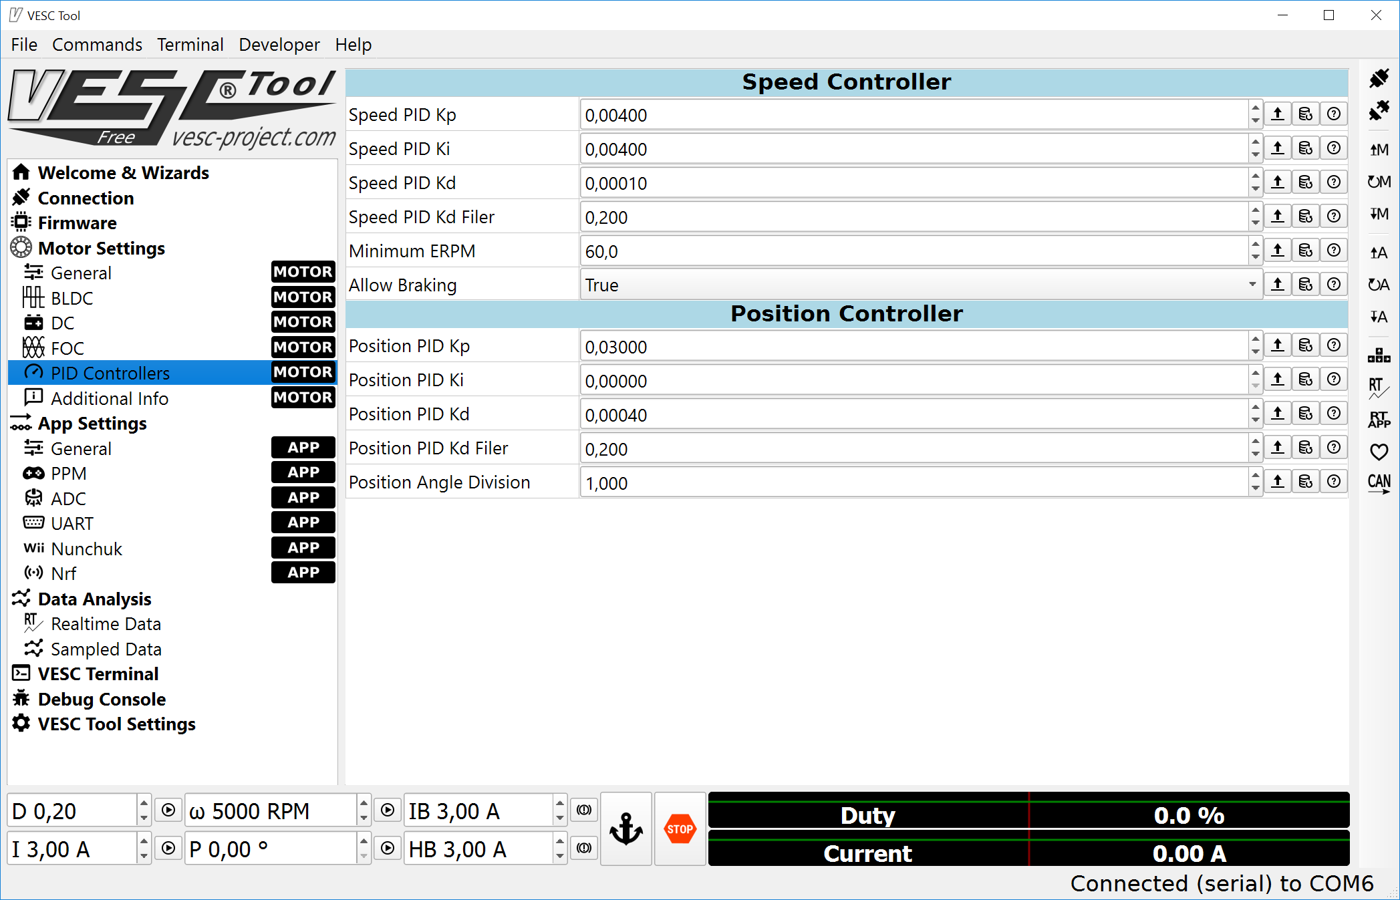
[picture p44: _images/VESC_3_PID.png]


#### Step 4 - Voltage Cutoff

To protect the battery the Vesc will turn off if the voltage falls below a certain value. Hence this needs to be configured. Simplest way is to choose the battery type and the number of cells - here LiPo with 6s (or more precise, 2x 3s LiPos in series) - and Apply copies the values.

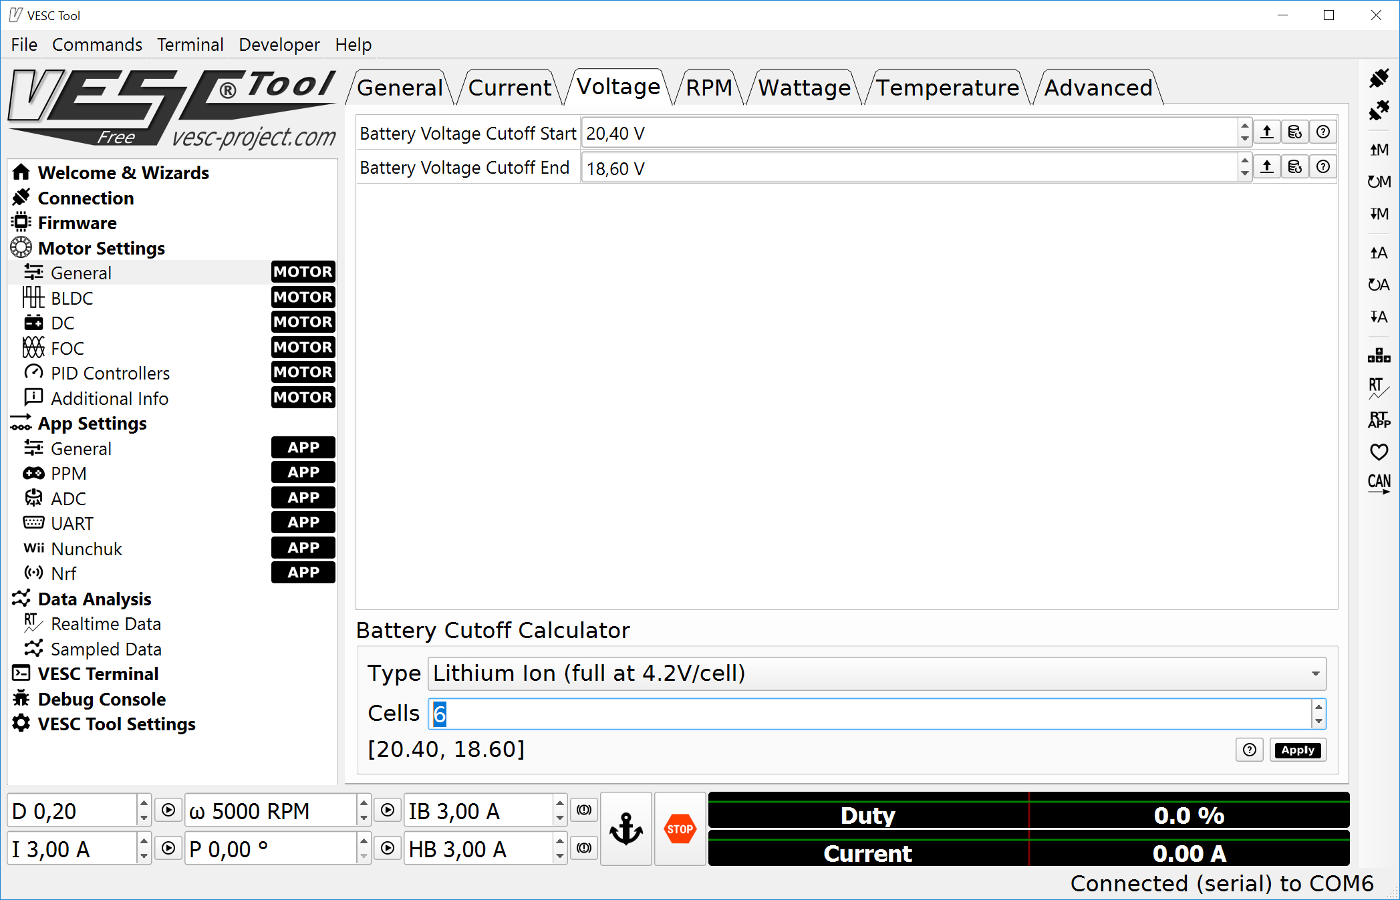
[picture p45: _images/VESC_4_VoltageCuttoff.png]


#### Step 5 - RPM Limit

The Vesc also has a ERPM limit for forward and reverse. Thsi should match with the motor specs or be lower than that. This value should also be at least as high as the \$e command shows. It does not make sense to put the stick into 100% forward, that translates to a Vesc speed command of e.g. 50'000ERPMs (the \$e value) but the motor is limited to less than that, does it?

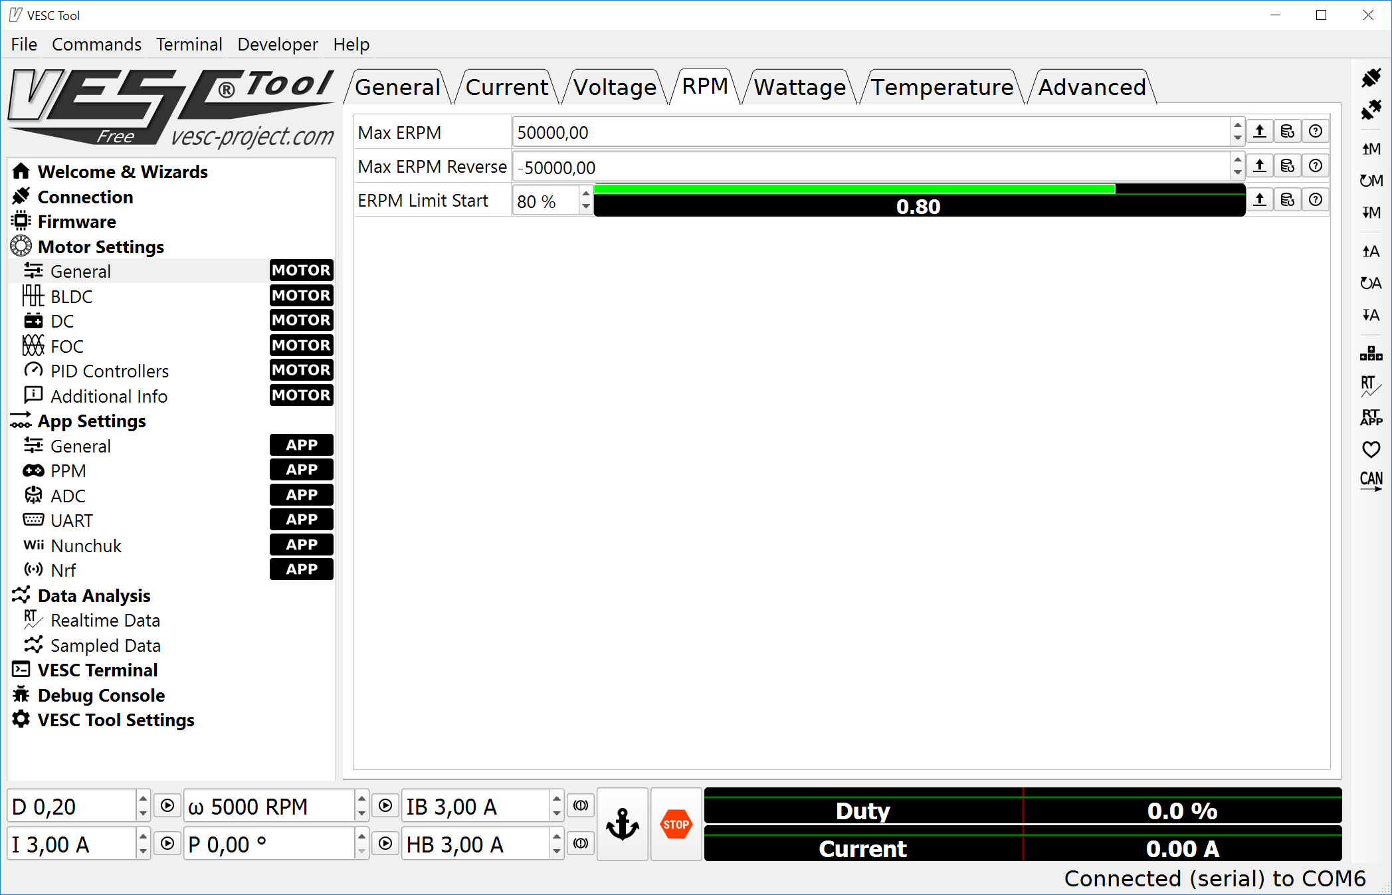
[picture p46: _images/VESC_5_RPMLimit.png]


#### Step 6 - Saving all to the Vesc and testing

If not done already, the motor settings should be saved to the Vesc using the right hand button list to save the configuration of the motor values.

Also there is a RT botton to start reading the values from the controller and displaying it in the Data Analysis -> Realtime Data graph. 

The controller supports different type of commands: Duty, Amps, Speed, Initial Brake, Handbrake. The P command is for moving the motor to a certain angle which is useful for a servo-like application only. It is not(!) a positional control in the sense of "drive 10 meters forward".

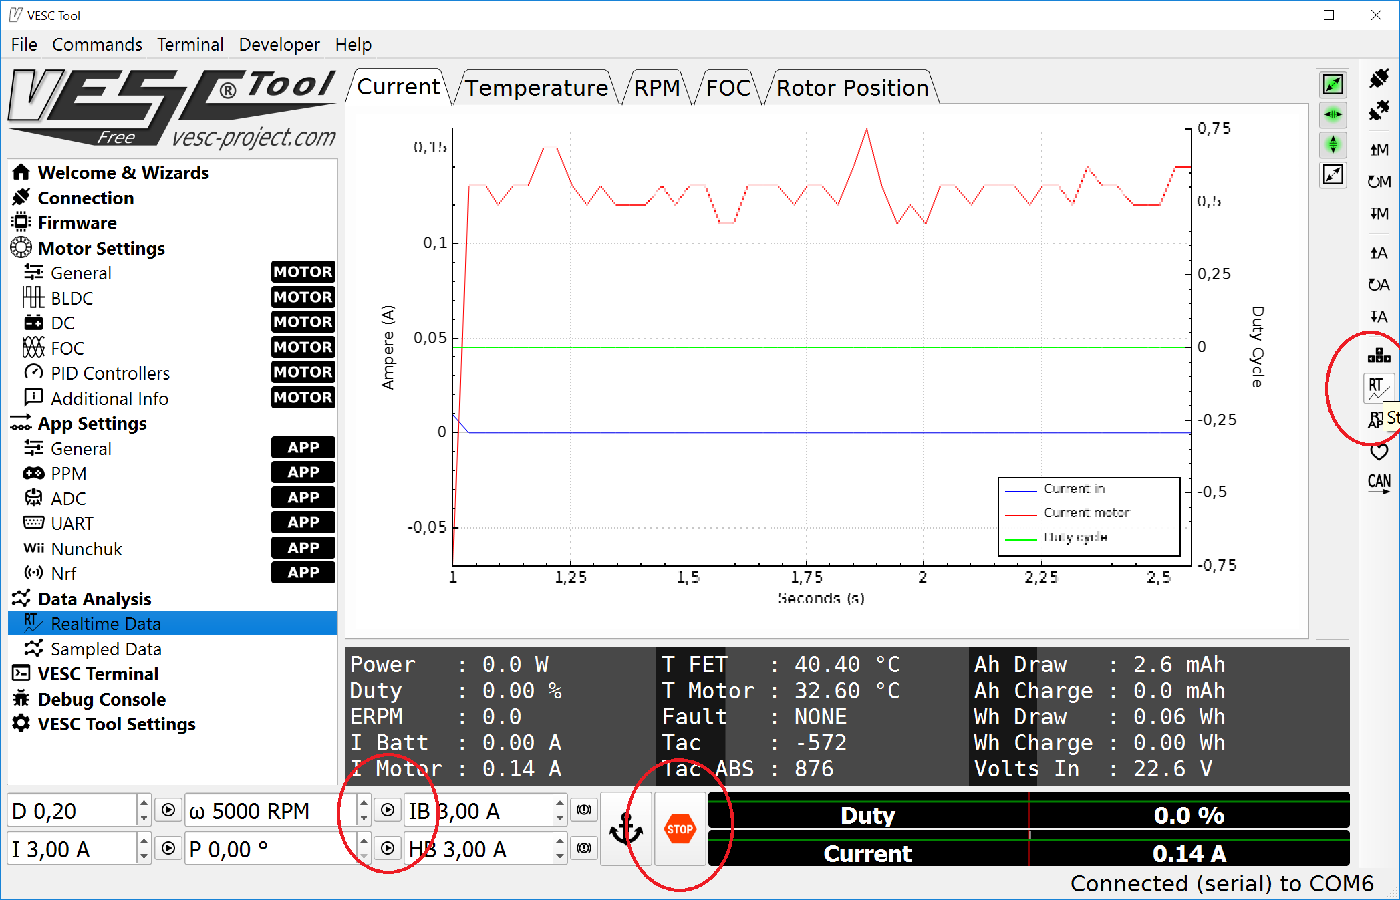
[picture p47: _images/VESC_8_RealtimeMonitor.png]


#### Step 7 - Input settings

The Vesc accepts commands from various sources, a servo signal, UART and other input devices. The CableCam controller can output a PPM servo signal but it is much better to control the Vesc directly via UART, hence this should be enabled as "APP to Use". 

This allows more accurate control as the target ERPM values are sent literally. And it allows to read the status values from the Vesc using the \$E command.

These App Settings have to be saved to the Vesc via the App button.

see [Connecting the Vesc](./Step%205b%20-%20VESC%20as%20motor%20controller.md) for the hardware wiring

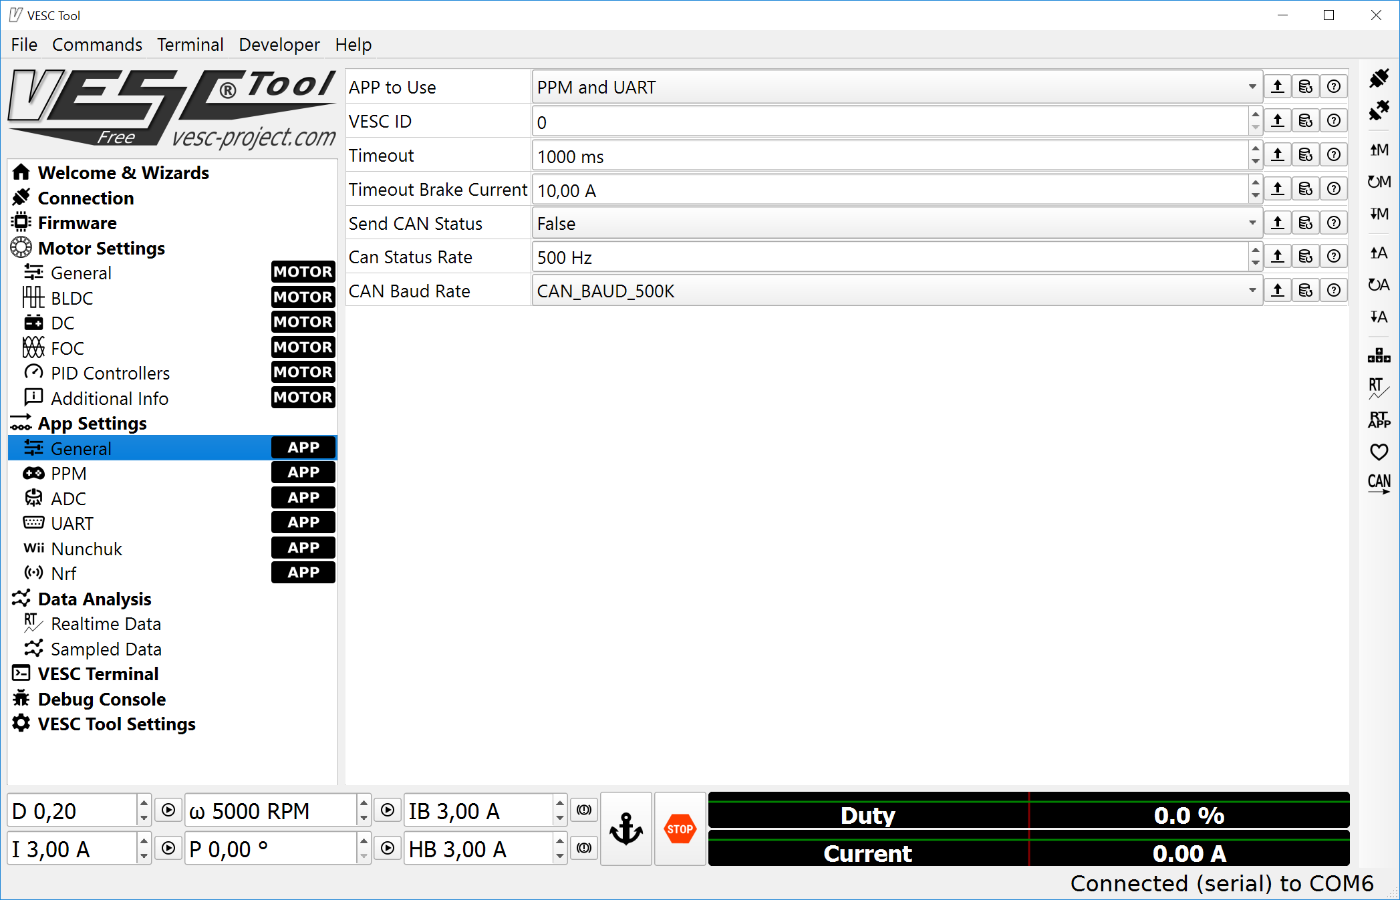
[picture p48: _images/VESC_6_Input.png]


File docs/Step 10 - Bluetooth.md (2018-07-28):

# Bluetooth/UART control

The controller supports getting commands via UART as well, usually connected to a bluetooth receiver like the HC-06. With that it is possible to change settings via an app, monitor the status via a serial bluetooth terminal, change settings on the spot.

## Hardware

#### MCU Pins used

| Function | MCU Pin | MCU Function | Connector Pin | Flip32 F4  |
| --- | --- | --- | --- | --- |
| UART TX  | PB10 | USART3_TX | FlexiPort/Conn1 Pin3 | J1 SCL/TX3 |
| UART RX  | PB11 | USART3_RX | FlexiPort/Conn1 Pin4 | J1 SDA/RX3 |
| GND | | | FlexiPort/Conn1 Pin1 | J6 GND |
| Vcc | | | FlexiPort/Conn1 Pin2 | J6 +5V |

#### Pinout

UART Pins

UART Pins

UART Pins

## Associated commands

| Command | Allowed values | Description |
| --- | --- | --- |
| \$B | | Run the HC-06 configuration wizard. Works with HC-06 bluetooth modules only. |
| $d b | | Turn on/off bluetooth debugging. Turned on means that all commands received from bluetooth are also printed on the USB terminal. |
| $d B | | Show the last errorcode for the UART3 where bluetooth is connected. Should help if the baud rate or related settings are configured wrong |

## Settings

The UART port is configured for 38400 8n1 and the bluetooth module needs to match that setting. How to change the settings is dependent on the bluetooth module being used.

The shown [Sparkfun Bluetooth Mate Gold](https://www.sparkfun.com/products/12580) is very convenient, it allows configuration of the UART port via the connected bluetooth device.

The more populare HC-06 module can be configured by AT commands. The HC-05 has an additional KEY Pin that needs to be dealt with. Details can be found in many places, e.g. [here](http://www.instructables.com/id/AT-command-mode-of-HC-05-Bluetooth-module/). As the HC-06 is so popular, the CableCam Controller has a command \$B that does configure it automatically via the USB terminal. Connect it to the board, make sure your tablet/computer is not connected with the HC-06 at the moment, because then it accepts AT commands from the UART side. The \$B command sends AT commands at various baud rates and when it gets a valid response, it executes the commands to make some changes. The command outputs the details about what it does.

On the tablet an app proven to work well is the [Serial Bluetooth Terminal](https://play.google.com/store/apps/details?id=de.kai_morich.serial_bluetooth_terminal).

## Which Bluetooth Module to use?

The majority of the bluetooth modules are Class 2 with a range of up to 10m. Not much for a cablecam. The [Sparkfun Mate Gold](https://www.sparkfun.com/products/12580) is one of the few Class 1 devices and has a supposed range of 100m.

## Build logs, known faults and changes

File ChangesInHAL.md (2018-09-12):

void HAL_UART_IRQHandler(UART_HandleTypeDef *huart)
{
   uint32_t isrflags   = READ_REG(huart->Instance->SR);
   uint32_t cr1its     = READ_REG(huart->Instance->CR1);
   uint32_t cr3its     = READ_REG(huart->Instance->CR3);
   uint32_t errorflags = 0x00U;
   uint32_t dmarequest = 0x00U;

  /* If no error occurs */
  errorflags = (isrflags & (uint32_t)(USART_SR_PE | USART_SR_FE | USART_SR_ORE | USART_SR_NE));
  if(errorflags == RESET)
  {
    if (__HAL_UART_GET_IT_SOURCE(huart, UART_IT_IDLE)) // DEal with idle flag
    {
      __HAL_UART_CLEAR_IDLEFLAG(huart);
      HAL_UART_RxCpltCallback(huart);
    }
    /* UART in mode Receiver -------------------------------------------------*/
    if(((isrflags & USART_SR_RXNE) != RESET) && ((cr1its & USART_CR1_RXNEIE) != RESET))
    {
      UART_Receive_IT(huart);
      return;
    }
  }

HAL_StatusTypeDef HAL_DMA_Start_IT(DMA_HandleTypeDef *hdma, uint32_t SrcAddress, uint32_t DstAddress, uint32_t DataLength)
{
  HAL_StatusTypeDef status = HAL_OK;

  /* calculate DMA base and stream number */
  DMA_Base_Registers *regs = (DMA_Base_Registers *)hdma->StreamBaseAddress;

  /* Check the parameters */
  assert_param(IS_DMA_BUFFER_SIZE(DataLength));

  /* Process locked */
  __HAL_LOCK(hdma);

  if(HAL_DMA_STATE_READY == hdma->State)
  {
/* Change DMA peripheral state */
hdma->State = HAL_DMA_STATE_BUSY;

/* Initialize the error code */
hdma->ErrorCode = HAL_DMA_ERROR_NONE;

/* Configure the source, destination address and the data length */
DMA_SetConfig(hdma, SrcAddress, DstAddress, DataLength);

/* Clear all interrupt flags at correct offset within the register */
regs->IFCR = 0x3FU << hdma->StreamIndex;

/* Enable Common interrupts*/
hdma->Instance->CR  |= DMA_IT_TC | DMA_IT_TE | DMA_IT_DME;
**// hdma->Instance->FCR |= DMA_IT_FE; // Disable FIFO error**

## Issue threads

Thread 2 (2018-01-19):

Flip32 F4 problem

addaedans, 2018-01-19:
Dear Werner Daehn!
We have a Flip32 F4 board and i flashed it with the latest firmware. We could flash it successfully but the serial console was nat available. So i rolled back and the last date that the firmware worked was 13 August 2017. From 14th the led won't flash on the board and the serial console is unavailable. Could you please help to figure out what is the problem? The project is really cool by the way, we are almost done with ollecting and cutting the parts.
Thanks,
Peter Bittó

wernerdaehn, 2018-01-19:
Hi Peter,

can you do me one favor: Please flash the board again, this time with the "verify after flash" checkbox ticked.
I am pretty sure the firmware file is okay as somebody else used it already and it does happen once in 30 flash processes, that it was not correctly uploaded - the verify would tell.

Deal?

wernerdaehn, 2018-01-22:
That other firmware did write some debug information for a test. So it was not meant to be a "release" firmware.
Okay, will stop checking in such intermediate firmwares from now on and distribute those via other means from now on.
I can look at the firmware file next weekend - hope that is okay.

addaedans, 2018-01-22:
Okay, thanks a lot.

addaedans, 2018-01-22:
I talked with the guys and we would have to use it at the weekend, so we are quite in a hurry. We realized it is the same as the airbot f4. It seems that the program won't even start on the chip, but it flashes successfully. Could you give us some hint what could be wrong with it? We may try to fix it in  the program.
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
Thanks,
Pete

wernerdaehn, 2018-01-22:
At the right bottom, there it say "boot". That should be the "switch".
Frankly I don't know why it does not start up. It says in the docs to that controller, that it is "compatible using the Revo target". So I assume the pinout is the same but that is no guarantee.
The MCU is the correct one, else you would very likely not have been able to flash it in first place.

Btw, this is the controller I bought:
https://www.getfpv.com/f4-advanced-flight-controller.html

And last comment: You understand that this cablecam controller is an option, not a mandatory component for operating the cablecam? It just acts as a filter between the RC receiver and the ESC to filter the user input in order to avoid hitting the endpoints, constant acceleration and the such.
Just to make sure, since you are under a time pressure....

addaedans, 2018-01-22:
Yeah we are in the same conclusion. It is the same thing but it still does not work...Yes we know that it works without it and we even tested it and works like a charm. But it will be on a pretty big event with quite a heavy camera + dji ronin system and the slow start and stop would be mandatory to avoid rope damage.

wernerdaehn, 2018-01-22:
Makes sense. How do you suggest to proceed? I could order such controller myself and try to find the difference. Or....... any ideas?

addaedans, 2018-01-22:
We just ordered another chip and hope it will arrive in time so we can test it as well. Maybe if you can modify the 13th of august firmware to print some basic information about the chip, it may show some evidence what goes wrong 1 day later. THan compare the 14th of august firmware with it and clean one half of the changes, than i test it. FOr the long run it would obviously be better if you buy one of this type of chip, but to start debugging this would be my idea, if it is possible.

wernerdaehn, 2018-01-22:
I will be back at my computer next weekend, maybe Friday.

wernerdaehn, 2018-01-25:
Sorry, overlooked the notification email to your last question.
No, no hardware needed. I use EmBitz 1.11 aus Software development environment, compile the software into a hex file and then use the STM "Dfu File Manager" to convert the hex into a DFU file.
That DFU file is then uploaded via the DfuSeDemo program from STM as described .

wernerdaehn, 2018-01-25:
Okay, I have ordered a board. Looks nice, actually.

wernerdaehn, 2018-01-26:
I have downloaded the dfu file from the bin/debug/ folder of this github page, uploaded it to my spare CC3D Revo board. Led is blinking, Console commands via USB are working.
The file is identical in every byte to the dfu file I built on my computer on 26th Dec and the one I am using since then.
So it is not the DFU file on the github page.
????

addaedans, 2018-01-26:
SOmething between this one:
https://github.com/wernerdaehn/CC3D-CableCam-Controller/tree/11146ff0d66414371e4624e285eb1fa255f23c92/bin/Debug

and this one:

https://github.com/wernerdaehn/CC3D-CableCam-Controller/tree/2633849a84b734728579d92d52165ffb0bd3318c/bin/Debug

has changed(i see a lot of update info) in one day. So the problem lies in some changes between these two files.

wernerdaehn, 2018-01-26:
Why are you using 6 months old files and not the one from December?
https://github.com/wernerdaehn/CC3D-CableCam-Controller/tree/master/bin/Debug

A lot of things have changed since then.

addaedans, 2018-01-26:
Because the 13th of August one is the latest that works with my chip. After that none of the firmwares are working.

wernerdaehn, 2018-01-26:
Understood. But that does not work either. Okay, you might get a firmware version that is running just not working properly as we enhanced the software a lot. The 14Aug was the first with RC input etc.

I have no idea why the firmware does not boot. No EEPROM chip?

addaedans, 2018-01-26:
We have this type of eeprom on the chip:

https://www.pjrc.com/teensy/W25Q128FV.pdf

It has some differences so it can be a problem.

wernerdaehn, 2018-01-26:
Likely, because I read the Flash Identifier and expect the same always.
https://github.com/wernerdaehn/CC3D-CableCam-Controller/blob/master/src/eeprom.c

And in the main I enter the error mode if it is not the correct one.
if (eeprom_init() != 0)
    {
        /* EEPROM is a wrong chip */
        Error_Handler();
    }

wernerdaehn, 2018-01-26:
Can you try out the version I just uploaded? I have changed the eeprom_init() to return success for all EEPROMs.

addaedans, 2018-01-26:
Thanks, i uploaded it and it seems to work. I reached the terminal as well, so try out the tutorial you wrote and write what happened.
Thanks :)

addaedans, 2018-01-26:
Oka i wrote some settings into the eeprom and it seems to work fine. We are at the final stage, and we have another question with the Hall sensors. Are the two sensors on the wheel take the signal simultaniously or in turns?

wernerdaehn, 2018-01-26:
Not sure I got your question. But the principle of a quadruple encoder is that the two Hall sensors both measure one magnet and the question is - which one got it first. So in a trivial world you would have two Hall sensors and a single magnet on the wheel and this way you can count the speed and the direction.
By adding more magnets the wheel appears to be turning faster to the Hall sensor.
This works as long as the magnets are not so tightly packed that the sensors measure the same signal but from different magnet.
And to play it safe, you use Hall senors that fire on North pole only and add the magnets north/south alternating to make sure the magnetic field strength falls below the sensor threshold - which it does for sure at the south magnet.
Answered?

addaedans, 2018-01-26:
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
So here is the HalSensor picture. My question is, that the blue line is the distance of the two hall sensors. The red line is the distance of 3 magnets(the distance of 2 magnets is too short for sure). So are the 1st and 3rd magnet on the red line fall below the two hall sensors or only one of the hall sensors sense the magnet at a given time. In programming language, if blue == red: print("Two sensors working at the same time")
else:
print("Only one sensor is working at a time")

:D

wernerdaehn, 2018-01-26:
You have it correct. The distance between the two hall sensors is e.g. 13mm and the distance between 1st and 3rd magnet is 16mm.
This works, because still one of the Hall sensors will pick up the signal of the north pole slightly before the other does. And with this time-gap the encoder can find out the direction.
Only once both distances would be equal, both sensors fire at the same time and the direction information is lost.

addaedans, 2018-01-26:
Perfect!
Thanks a lot for the help. We are going to make a short footage made with the cablecam, i will send it for you if interested.
Thanks again :)

wernerdaehn, 2018-01-26:
Absolutely! Looking forward to it.

Closed 2018-02-11.

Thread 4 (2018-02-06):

Trying to make it work with other components

mitarashki, 2018-02-06:
Hello Werner.
First of all I would like to thank you for sharing this amazing system to all of us. It is a great way to film with cable cam more safely. I really appreciate your work. Thanks again

mitarashki, 2018-02-06:
I am currently trying to make your system work with a bit different components like:

1) Instead of using ESC I am with : https://www.pololu.com/product/1372
 It is a DC brushed motor controller
2) Instead of using Hall sensors I am using 500 P/R encoder connected the same way to the board like you described it for Hall sensors

Because I am not really a software guy I would like to ask you some questions about the problems I experience with my setup.

I am to a point where everything works but not exactly like expected :)
When I power on the system its all good. I enter program mode where everything works fine (ex. motor is moving smooth in both directions, position 1 & 2 is recorded successfully)
When I  switch to "Operation mode" and give command above the end point it does not move (like it have to be), but when a command for moving to the first end point is given the motor starts spinning in pulses (not smooth) and when it reaches the end point stops. Also when applying command in "Operational mode" in the PuTTY lot of lines saying "Endpoint brake on" are displayed.
If there is a possibility for you to help me with my problem I would be very grateful.

The other components I am using are:
-Airbot F4 MPU6000
-S.bus receiver paired with Spektrum DX7s
-60V DC Brushed motor

Thank you very much in advance Werner.

wernerdaehn, 2018-02-06:
I am having troubles grasping the problem. Can you create a short youtube video?

One thought I have is the $r command, the rotational direction. But this is important only when you are over the end point. And that does not sound like your problem.

mitarashki, 2018-02-06:
OK Werner, I will do it tomorrow morning and will send you the link. Thanks a lot for helping.
Do you think that using a high resolution encoder instead of hall sensor might be a part of the problem?

wernerdaehn, 2018-02-06:
We might find issues, but not the ones you are describing. No, would not expect that.

Reading your text again, maybe it truly is the $r command. Can you do me a favor and check what it is set at the moment? And reverse it. So from +1 to -1 or vice versa.
I have checked the code sequence around the "Endpoint brake on". It checks if the current position according to the hall sensors plus/minus the calculated brake distance would go beyond the start or end point. If yes, it does engage the brake.
Trouble is, if you are very close to one of the endpoints but driving **away** from it, above logic would still kick in the brake. So the controller needs to know if the current stick position drives the motor towards or away from the end point. That is what the $r command controls. Is a positive stick a movement towards the start or the end point.

Now imagine it would be the wrong value and you are close the end position. You start driving away, pick up some speed and now the calculated brake distance is high enough so that pos + brake distance > endpoint. Brake kicks in. Until the speed is low enough so that above condition is no longer met. It would accelerate again.
With the correct $r value the controller would see you are driving away from the end point and hence test for the start point only.

mitarashki, 2018-02-06:
It sounds to me that this might be the problem because I was trying it with just 5-10 rotations of distance between the two end points which is probably too close. I have already tried to change the $r value but there was no change in the behavior of the motor. Now it is set to +1.
I will be back tomorrow morning in my workshop and try to set the end points with bigger distance between. Will update you with the result as soon as make the test.

-I am also wondering what might be the right value for $g, considering that I am using 500 steps per revolution?
-When $p is applied it shows 1-----0-----0 . Is that what should be displayed

wernerdaehn, 2018-02-06:
If $g would kick in, the console would say "Emergency brake".  This $g is just a failsafe. Imagine something is totally wrong and slowly moving the virtual stick to zero does not have the effect of slowing down the cable cam. Then the controller gives up on everything and screams: Speed=0. Now. And hopefully the ESC stops the cable cam then.

$p is certainly wrong. It appears the start and end position is one and zero. Actually, there is something fishy, if that is the readout you get. The code reads:
`    case PROTOCOL_POS:
        writeProtocolHead(PROTOCOL_POS, endpoint);
        writeProtocolLong(activesettings.pos_start, endpoint);
        writeProtocolLong(activesettings.pos_end, endpoint);
        writeProtocolLong(getPos(), endpoint);
        writeProtocolDouble(getSpeedPosDifference(), endpoint);
        writeProtocolDouble(getSpeedPosSensor(), endpoint);
        writeProtocolOK(endpoint);
        break;
`

mitarashki, 2018-02-07:
https://youtu.be/IXC9dJT70Vg
Hello Werner.
That is the link with the video of my problem.

wernerdaehn, 2018-02-07:
After you have programmed the end points, what does $p say?

mitarashki, 2018-02-07:
After recording the two endpoints, $p says -1   -1   -1

wernerdaehn, 2018-02-07:
Encoder obviously does not update the position.
Any idea why?

mitarashki, 2018-02-07:
I have just tried 3 different encoders:
#1 1024 steps/revolution
#2 500 steps/revolution
#3 100 steps/revolution

After recording the end points in programming mode successfully the $p says always one of those:
1  1  0 or -1  -1  0 or 0  0  1 or -1  0  0 never goes over 1 or below -1

I have no idea why is that happening. Any idea what I should try ?

wernerdaehn, 2018-02-07:
Since the value does change, it does get signals. Let's assume that for a minute.
Can you use the 100steps encoder and move it by hand very slowly. I'd like to know if the frequency is too high for it to recognize which input comes first.

I am not using any prescaler, filter or anything else. So it should not be that.
Do you have an osscilloscope with two channels to see how the two pulses relate to each other?
And the data sheet of your encoder might reveal something.

(main.c)
    htim5.Instance = TIM5;
    htim5.Init.Prescaler = 0;
    htim5.Init.CounterMode = TIM_COUNTERMODE_UP;
    htim5.Init.Period = 4294967295;
    htim5.Init.ClockDivision = TIM_CLOCKDIVISION_DIV1;
    sConfig.EncoderMode = TIM_ENCODERMODE_TI12;
    sConfig.IC1Polarity = TIM_ICPOLARITY_RISING;
    sConfig.IC1Selection = TIM_ICSELECTION_DIRECTTI;
    sConfig.IC1Prescaler = TIM_ICPSC_DIV1;
    sConfig.IC1Filter = 0;
    sConfig.IC2Polarity = TIM_ICPOLARITY_RISING;
    sConfig.IC2Selection = TIM_ICSELECTION_DIRECTTI;
    sConfig.IC2Prescaler = TIM_ICPSC_DIV1;
    sConfig.IC2Filter = 0;
    if (HAL_TIM_Encoder_Init(&htim5, &sConfig) != HAL_OK)
    {
        _Error_Handler(__FILE__, __LINE__);
    }

    sMasterConfig.MasterOutputTrigger = TIM_TRGO_RESET;
    sMasterConfig.MasterSlaveMode = TIM_MASTERSLAVEMODE_DISABLE;
    if (HAL_TIMEx_MasterConfigSynchronization(&htim5, &sMasterConfig) != HAL_OK)
    {
        _Error_Handler(__FILE__, __LINE__);
    }

mitarashki, 2018-02-07:
That is the datasheet of the encoder:
https://www.mouser.com/ds/2/678/V02-1046EN_DS_HEDM-55xx_2014-11-20-909010.pdf

I have tried moving it slowly by hand and it says again 0  1  0

wernerdaehn, 2018-02-07:
Do you supply it with 5V or 3.5V? It needs 5V.
Are you using Ch.A plus Ch.B and not Ch.I as input to the cable cam controller?

mitarashki, 2018-02-07:
Yes I am using Ch.A & Ch.B as input to the cable cam controller but the supply voltage is 4.3V not 5V. My motor controller output is 4.3V
Is this a possible reason for the problem?

wernerdaehn, 2018-02-07:
Unlikely but not impossible. Your encoder has an active circuit and it says as Recommended Operating Conditions: 4.5 to 5.5V.
But as said, will work with 4.3V as well. On the other hand, what else?

Just to doublecheck, can you make photos so I can see the electrical connections from the encoder to the cable cam board?

mitarashki, 2018-02-07:
This a test I did with the 100steps encoder using two light diodes and resistors
https://youtu.be/AhPSVrRC7mA
I will send you pictures in a minute

mitarashki, 2018-02-07:
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

wernerdaehn, 2018-02-07:
Hm. So it is not the encoder and the used pins are correct as well. What else could it be????

You have connected the LED with +5V and the yellow resp. white cable. So whenever the encoder pulls the yellow/white cable to GND the LED emits light. An opencollector circuit just like my Hall sensors have.

Let me solder a header to your flight controller, I got one meanwhile as well, and simulate the position input via switches. This will give us a another point of proof to isolate the issue.

If you have an idea, please let me know. I am a bit baffled at the moment.

mitarashki, 2018-02-07:
Please excuse me but I couldn't understand that :
"Let me solder a header to your flight controller, I got one meanwhile as well, and simulate the position input via switches. This will give us a another point of proof to isolate the issue."

wernerdaehn, 2018-02-07:
Sorry, mixed up two conversations.
Let me put it this way: I's like to setup a test for you to follow in order to check if the problem is before the cable cam controller or within.

wernerdaehn, 2018-02-07:
I have a second board that looks just like yours. Because of another issue we had previously.
http://www.readytoflyquads.com/flip32-f4

I have programmed the firmware and tested the servo5&6 with switches and did not get position update either. Hence I measured if servo5=PA0 and servo6=PA1. Yes for servo5 but **servo6 is connected to another pin** on the MCU. The PA1 pin is connected to a pad on the other side's 3x9 header, the pad  exactly in the middle of it.
If I use that, the $p shows position updates.

So to cut a long story short: Hardware looks similar but the connector layout is not identical. Good to know.

mitarashki, 2018-02-08:
OK, I am doing a test right away. Is that the correct pin for PA1 ?
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

wernerdaehn, 2018-02-08:
No, one step to the left. It is really the center one, with four holes above and below and one hole left and right.

mitarashki, 2018-02-08:
Hey Werner. Thank you very much for your great support.
Now everything works perfect. I have tried it with two different encoders (100 S/R and 400 S/R) and with both of them the systems works. Thank you again.
I am starting to assemble my cable cam and when it is all together I will keep you updated for the results on the rope.

I really appreciate you help end effort.

wernerdaehn, 2018-02-08:
Yipeeeh! ;-)

mitarashki, 2018-02-08:
**YOU ROCK MAN** :+1:
:)

Closed 2018-02-11.

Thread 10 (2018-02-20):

Just burned a motor controller

mitarashki, 2018-02-20:
Hello again Werner
I have just burned a RoboClaw 2x60AHV, 60VDC Motor Controller
Link: http://www.ionmc.com/RoboClaw-2x60AHV-60VDC-Motor-Controller_p_12.html
Dtasheet: http://downloads.ionmc.com/docs/roboclaw_datasheet_2x60AHV.pdf

I know it was not a problem that came from the CC3D board or software and I am just looking for a help to figure out what happened.
Everything was running fine on a 6S (25.2V) LiPO battery until I have decided that it is ready to be tested on a 12S (50.4V) LiPO. Once I plugged it to the power it burned into flashes and smoke (ouch). This model is rated up to 60V,60A per channel and I ran it in "Bridged" mode which doubles the output to the motor to 60V,120A.

I am just looking for your opinion what may be the cause of the burn. I am sure it was wired correct, but not sure that I have it properly tuned.
Please excuse me for bothering you with my problems.

Thank you very much in advance for your support

wernerdaehn, 2018-02-20:
Can we discuss that somewhere else?
Maybe here?
https://www.rcgroups.com/forums/showthread.php?2103895-Cable-Cam/page9

mitarashki, 2018-02-20:
Yes sure

Closed 2018-02-20.

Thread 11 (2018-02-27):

Bluetooth connection

Willyfan, 2018-02-27:
HI Warner, I tried to connect a bluetooth module, it is not claer as setup it. I seen a images where you also changed the hall sensor IN. Can you help me?

wernerdaehn, 2018-02-28:
What board do you have precisely? The white one like I used originally?
It has the servo ports at one side - and, I have not changed anything there - and some more pins on the other edge. The top ones called TX3/RX3. These are the bluetooth pins.
Next step is to enter the command $B to autoconfigure the bluetooth module.

Willyfan, 2018-02-28:
Hi Werner, thanks for your answer.I have the new board, the same you have in the image directory with indicated Bluetooth pin. About Bluetooth, i solved because I found the command for configuration. It's OK ant it work.But I seen in the new image that you moved the input of one of hall sensor to the other side of the board. I will send you the pics later, now I'm on phone.Il 28 feb 2018 11:07, wernerdaehn <notifications@github.com> ha scritto:What board do you have precisely? The white one like I used originally?
It has the servo ports at one side - and, I have not changed anything there - and some more pins on the other edge. The top ones called TX3/RX3. These are the bluetooth pins.
Next step is to enter the command $B to autoconfigure the bluetooth module.

—You are receiving this because you authored the thread.Reply to this email directly, view it on GitHub, or mute the thread.

wernerdaehn, 2018-02-28:
I have not so much moved the Pin of the hall sensor, it is rather that this Servo6 Pin is actually not Servo6 on the board.
To be more precise: PA0 and PA1 are Servo5&6 on the white PCB but routed differently on the Flip32.
https://github.com/wernerdaehn/CC3D-CableCam-Controller/blob/master/_images/FLIP32-F4.jpg

kornel508, 2018-03-07:
Dear Werner!

I would like to upgrade my FPV (white PCB) with bluetooth module. Succesfully wiring the panel, but in the terminal after $B command i get an error. No response.....
I try the module to program with AT commands from an Arduino Uno. It's working good.
But from the FPV isn't working. What could be the problem? Thanks for your help!
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

Willyfan, 2018-03-07:
Are you sure that the module is powered? In pictures I don't see the led light... But as is blinking, maybe the picture took the off state. Il 7 mar 2018 09:46, kornel508 <notifications@github.com> ha scritto:Dear Werner!
I would like to upgrade my FPV (white PCB) with bluetooth module. Succesfully wiring the panel, but in the terminal after $B command i get an error. No response.....
I try the module to program with AT commands from an Arduino Uno. It's working good.
But from the FPV isn't working. What could be the problem? Thanks for your help!

—You are receiving this because you authored the thread.Reply to this email directly, view it on GitHub, or mute the thread.

wernerdaehn, 2018-03-07:
I would have the same immediate idea. Most of the pins supplying +5V or Vcc on the CC3D Revo are not powered by USB. So when you try to use the Bluetooth module, does the controller get power from e.g. the ESC? Or is it USB only?
Easy to find out, the HC-05 has a status LED that blinks while nothing is connected. Does it blink?

kornel508, 2018-03-07:
Thanks for your fast answer! Of course, the power LED blinks.
There is a button on the upper left corner of the PCB, this is the programming mode switch. I hold this button when i powering the boards to step into the programming mode...
All function working from an Arduino. Please write how to program the Bluetooth module?
AT+ORGL
AT+NAME=CABLECAM
AT+PSWD=1234
AT+UART=38400,0,0

Is this correct for the communication?
Thanks!

Kornel

wernerdaehn, 2018-03-08:
AT+BAUD6
AT+NAMECableCam
AT+PIN1234
refer to [bluetooth.c](https://github.com/wernerdaehn/CC3D-CableCam-Controller/blob/master/src/bluetooth.c)

Seems you do not have a HC-05?
Anyway, if you configure the BT module by hand and connect it, it should work right away. 38000,n,1 is the UART3 config.

```
static void MX_USART3_UART_Init(void)
{
    huart3.Instance = USART3;
    huart3.Init.BaudRate = 38400;
    huart3.Init.WordLength = UART_WORDLENGTH_8B;
    huart3.Init.StopBits = UART_STOPBITS_1;
    huart3.Init.Parity = UART_PARITY_NONE;
    huart3.Init.Mode = UART_MODE_TX_RX;
    huart3.Init.HwFlowCtl = UART_HWCONTROL_NONE;
    huart3.Init.OverSampling = UART_OVERSAMPLING_16;
    if (HAL_UART_Init(&huart3) != HAL_OK)
    {
        _Error_Handler(__FILE__, __LINE__);
    }
}
```

kornel508, 2018-03-08:
I have lot of HC-05, but your commands is for HC-06, this is a difference in AT comannds and HC06, it does not wait for any termination character for each AT command entry, HC-05 wait NL & CR after command.
HC-05 is an universal type for master and slave mode. HC-06 is a fixed slave mode device...
http://www.instructables.com/id/AT-command-mode-of-HC-05-Bluetooth-module/

wernerdaehn, 2018-03-08:
Okay, thanks for the correction. Given that the behavior is completely different, you have to press a button, commands are different, <CR><LF>, etc.... what is your suggestion?
I will obviously update the documentation but do you want to see more than that? Or are you okay configuring the HC-05 externally and just connect it?

Sorry for the confusion.

Willyfan, 2018-03-08:
I wrote a app, working (only android) for checking and programming by Bluetooth, please let me k ow if you want try it. Il 08 mar 2018 22:26, kornel508 <notifications@github.com> ha scritto:Dear Werner! No problem, I program manually the HC-05 with the good commands from your comments and working good. Thanks for your help!
At weekends I would like to make a simple GUI application, for easy programming and position checking.
Best regards
Kornel

—You are receiving this because you authored the thread.Reply to this email directly, view it on GitHub, or mute the thread.

kornel508, 2018-03-09:
Of course I would like to try it. But, IOS version would be more pleased. :) I know the HC-05 not work with Apple phones...
Thanks!

wernerdaehn, 2018-03-09:
Me too, but Android is fine. If you need more/different commands in the CableCam controller, let me know.

cofhal, 2018-03-09:
Dear Willyfan
Is possible public the APK for programming the CCD3.

Willyfan, 2018-03-09:
Yes, I'll upload the apk in the night on my server, and give you a link. Sorry for the late in reoply, but I was out office for production.
The app, I'm sorry, is only for android. And plaese, test it and give me a feedback, is a "beta" but it seems workwell.

Willyfan, 2018-03-09:
http://william-fanelli.com/wp-content/uploads/myupload/ID_CablecamSetup_5.apk

Please check it, let me know. Foe now, I don't need different command, but a OFFSET for limits can be useful.

Willyfan, 2018-03-11:
I re-uploaded now the file, because I found a bug in channel assignement. If someone just downloaded, please re-download (last upload at 11/03/2018 16:00  )

wernerdaehn, 2018-04-02:
Can you please check your app with the firmware I just uploaded? I made a couple of minor changes in the protocol and have the fear, depending on the logic you use, the app might not parse it correctly and needs slight tweaking hence.

Willyfan, 2018-04-02:
I will test it tomorrow in the afternoon. But I took a look at the your updated commands table, In my opinion the app work but I will test. I don't use the $j command, but all the old command should be work.

wernerdaehn, 2018-04-02:
It is things like trailing blanks got removed from decimal numbers, e.g.
before '   0.00' and now '0.00'.
Or in $i I changed it that the OK comes before the channel assignments are printed in detail. Before all text was part of the command return. Now it is just the $i line with the channel list and the details are printed as extra text.

Willyfan, 2018-04-03:
Hi Werner, the app still work. Please explain me how work the automatic mode, so I can write additiobnal command to the app. Beside, a command for read fw version will be useful in order to mantain backward compatibility.

wernerdaehn, 2018-04-03:
https://github.com/wernerdaehn/CC3D-CableCam-Controller/issues/16#issuecomment-378088628

Closed 2018-05-13.

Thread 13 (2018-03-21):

flashing the firmware on CC3D EVO

TillMack, 2018-03-21:
Hi Werner,
I have an issue flashing the firmware on my CC3D EVO board.
Connecting the board, while keeping the boot button pressed ( unfortunately the board doesn't have a boot button, but a solder-pad-bridge), starts the internal USB bootloader. Shown by the Power LED, which is on and the Status LED, which is off.
But for some reason the board doesn't appear in the DfuSe utility at all.
I've done this procedure a couple of times, but the board never showed up in the DfuSe utility.
Do you have an idea how to solve this problem?
Or know what I am doing wrong?

Regards,
Till

wernerdaehn, 2018-03-21:
I fear the CC3D EVO is a CC3D (STM32F1 based) and not a CC3D REVO (STM32F4 based).
https://www.reddit.com/r/Multicopter/comments/3f5r3f/cc3d_evo/

No surprise that it does not show up in the DfuSe tool. The STM32F1 does not have a bootloader wired in the MCU.

TillMack, 2018-03-21:
All right, didn't know there is a difference between these two boards regarding the STM32.

Makes totally sense.
So I'll better get a CC3D REVO.

Thank you for your fast reply.

Closed 2018-03-21.

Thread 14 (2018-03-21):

broadcast to the Servo2 output

zond-media, 2018-03-21:
Thank you for this wonderful project!
Can you add the ability to broadcast directly 1 channel (any free) from the transmitter to the second output of the board (Servo2)? That would be great!
Plan to put the Servo to control Yaw on gimbal.

wernerdaehn, 2018-03-21:
That's actually a good idea. I have a similar request for a break-servo and was wondering how to incorporate that. Answer is simple: Use the RC sender mixer.
Will do.

zond-media, 2018-03-21:
in the case of a Brake use a Mixer is of course a good idea, but in my case it does not fit at all.
Thank you, looking forward to the implementation ;)

zond-media, 2018-03-22:
as another proposal ;)
It would be cool to have an automatic mode so as not to touch the throttle stick!

wernerdaehn, 2018-03-22:
btw, what gimbal are you using? Just out of curiosity...

wernerdaehn, 2018-03-25:
I just went through the hardware layout and the code, servo2 actually is configured for PPM servo output already, just like servo1 for the PPM ESC output. Hence to enable what you requested is essentially one line of code or so.

My problem is the $i command as such. Currently it takes as parameters

- ESC channel
- programming switch channel
- endpoint button channel
- max acceleration dial channel
- max speed dial channel

And now I add the aux channel, later the yaw, pitch, tilt channels for the gimbal and more. I think I want to change that and rather move the accel and speed channel settings to the corresponding commands $a and $v. Likewise with the aux and gimbal channel settings. Move those to commands of their own.

Agree? Leave $i as is but move he future gimbal channels to something else? And Aux to $i or to the gimbal commands?

I am undecided what's best.

zond-media, 2018-03-25:
I think that the best option to place commands for gimbal or aux into a separate group. for example $G
I'm sure this will be the right decision.

wernerdaehn, 2018-03-25:
Agree. Nevertheless, because the Aux Output can be used for Yaw and Brakes, I thought I better add that as yet another $i parameter. That does not prevent us to assign the value via other commands as well or do like suggested for the full gimbal control.

Regarding Gimbal Control I am preparing everything to use another Pin as SBus out. Unfortunately the Revo board has a single SBus Inverter only (none on the TX pin), hence we need another piece of hardware for that. Too bad.

zond-media, 2018-03-25:
**wernerdaehn**, thanks!
and what about Automatic Mode? ;)
Can I open new Issue?

wernerdaehn, 2018-03-25:
Can you elaborate on what you mean with automatic mode? This is related to the break as opposed to the initial inquiry of yaw control, isn't it?

zond-media, 2018-03-25:
I mean automatic CableCam movement at a given speed back and forth without moving the gas stick with the start and end position. This mode is needed for working alone, so that there is a possibility of controlling the gimbal.

wernerdaehn, 2018-03-26:
Yes, a new issue please.

zond-media, 2018-03-26:
Ok

Closed 2018-03-26.

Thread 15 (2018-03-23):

Speed and acc.

Willyfan, 2018-03-23:
Hi, now I'm trying for the first time the controller, and with my cablecam I have a problem with speed and acceleration.
In passtrough mode is ok, but I don't have limits.
In passtrough with endpoints, the response of the motor is not good. When I put the stick in one direction, it accelerate very slow (I tried many setting for this) and when I release the stick, it decelerate very slow, too slow.
If I rotate at max value the pot for max acc and max speed the situation is better, but not good.
Question is: is possible, when pot is at max value, have the same response as passtrough?
The problem is that on short cable (under 15 metres), I'm unable to reach good speed before end point.
Regards
William

wernerdaehn, 2018-03-24:
I have made some changes last month and the acceleration - using the poti on the RC sender - so that min acceleration is 20 secs from 0 to 100% and the maximum 2 secs.

Now we need to find out what it is. Is it that everything works fine but the 2 secs is a too little max value?
Is it the poti range?

Can you set the potis to max speed and max accel and give me the readings for $a and $v?

Keep in mind, if you change your input so that the potentiometers are not used, you can set any value for $a. Might be worth a test.

Willyfan, 2018-03-24:
Hi Werner, thank you for your reply .
I done some test. If I disable POT, I'm able to set all value from 0 to 0.999 for acceleration, in Programming and Operational mode.
With POT, after setting at best the max deflection, I'm able to have value from 0 to 0.500 (no more) and pot work only in operational mode (reading the value from putty with $a command). Programming mode say always as set by $a command.
With this value the acceleration and the deceleration are too slow in some cases. Also the value set to 1 with POT disabled have a deceleration too slow in some cases, but it can be accettable.
So, I think that a modification of the code can be extend the POT value range from 0 to 1 and not from 0 to 0,500. Or, if is possible, the POT set the value from 0 to max value setting ($a). In this way, You can limit anyway the MAX acceleration and deceleration, but if you need you can have a wider range.
I think that the same can be applied to speed, but I must do some other test for speed.

wernerdaehn, 2018-03-25:
No problem doing that. But before I do that actually, let me ask a few questions.
A setting of 0.5 means 2 second ramp from 0 to 100% speed. A setting of 1 means one second. Isn't that a bit aggressive?
Assuming it is all fine, why can your cablecam accelerate so fast? Do you have such a low max speed or better components?
What ESC are you using? VESC via UART or a regular ESC via Servo1 (PPM output?)

wernerdaehn, 2018-03-25:
Okay, new firmware allows to change $a from 0 .05 to 1.00 via the RC.

Willyfan, 2018-03-27:
Thank you, now I will try. Anyway, I noticed that my problem is not the acceleration (also 2 seconds and more can be good) but sometimes the deceleration, because when you release the stick the cablecam move for other 2-3 or more seconds. Sometimes is too much.

wernerdaehn, 2018-03-27:
Okay. Makes my question regarding "What ESC are you using" even more important.
Take the VESC for example, as this has a PID closed loop for speed. Even here it does not help much if I tell the VESC to reduce the RPMs to zero in 2 seconds, if the physics or the PID settings do not allow for that. Imagine the cablecam 50kg heavy and a 1kW motor. No way it can break that quickly.

And the cablecam controller has no way of knowing that. The only thing I can do is a failsafe: When the breaking is not powerful enough and the end point is overshot significantly, forget about the ramp and brake as hard as the ESC can. In case of the VESC that means setting the speed to zero, in case of the PPM output setting the speed signal to neutral.

Willyfan, 2018-03-27:
You are right: for now, at the question "what ESC" my answer is a XERUN xr8 (tried sensored and not sensored, little difference). I want try a VESC that I have at home, but for now is a bit experimental. I hope that I will find time after 15 april for this test on VESC.
Now, I updated my board with new firmware, I will test on cable tomorrow morning.

Willyfan, 2018-03-27:
Dear Werner, i noticed that beside to acc modifications you added 2 parameters to input channel mapping. I read that one is for AUX, and the other? I will modify the android app for this. Have you tried it? Anyway, old version still work, but ignore thet parameter.

wernerdaehn, 2018-03-27:
The last one is the channel for the Aux output. The one before last is the channel to switch between Passthrough, Limiter, Limiter+Endpoints via the RC.

No, haven't tried the app yet.

Willyfan, 2018-03-27:
Ok, I will add also the last parameters as soon as possible.
I can use a 3 way switch for the last switch? What values it need from RC?

wernerdaehn, 2018-03-27:
Exactly, a three way switch with high, neutral, low as signal sets the three modes.
(When USB or BT is connected, flipping the switch writes an event text. You can use that to validate.)

Willyfan, 2018-03-27:
Ok, It work.  I uploaded a new version of android APP, same link as before.
I added the new parameters, and a continuos reading of message from cablecam, so you can read swich alert. About acceleration, now is better controlled. Anyway, tomorrow morning I will test on cable.

Willyfan, 2018-03-28:
Tested on cable this morning, I'm very happy. Now response of the cablecam is very good also at low speed. Acceleration have no problem at max, but I checked also with pot at mid position, is ok.
When speed is hight, the cam overshot the limits: need to be a bit "conservative" when setting the limits and use high speed.

Willyfan, 2018-03-28:
I agree, this is a good setting.  Maybe better precision can be obtained with a  logaritmic curve, but I can set it on the transmitter, no problem.

wernerdaehn, 2018-04-04:
Got a request from somebody else to change it yet to another value. As can't do it right for anybody, I revised the logic.
With $a 0.500 0.050 you set the absolut max values in Operational and EndpointProgramming mode: 1/0.5=2 seconds from 0...100% and in safemode 1/0.05=20 seconds from 0...100%.
With the poti then allows you to scale the actual max accel between 0 (almost zero) and this programmed max.

Speed is the same thing, use $v 1.000 0.250 to limit the speed stick movement and the poti then scales it further down. Here the logic makes a little less sense, why would you set the speed limiter in normal mode to anything other than +100%??? And the minimum speed is certainly not almost zero but 20%.

wernerdaehn, 2018-04-22:
After another chat, I changed the speed logic again. Before a speed limit of 50% meant every speed movement >50% was unused.
Now the stick can be moved unlimited but the speed limiter is applied to the output.
Example:
Servo 1 output: Max speed of 50% means the the output signal moves between 1500+-400 instead of 1500+-800 (or whatever the precise numbers are in $N).
VESC Uart Output: Max speed is 50% of the max erpm value configured ($e).

As a result the stick can be used at full range to control the speed between +- max speed.

wernerdaehn, 2018-05-13:
I am closing this as DONE.

Closed 2018-05-13.

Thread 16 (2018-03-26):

Automatic Mode

zond-media, 2018-03-26:
add a new mode: automatic cablecam movement at a given speed (by the Pot via RC or(and) variable in settings) back and forth without moving the stick with the start and end position (set before). This mode is needed for working alone, so that there is a possibility of controlling the gimbal with another RC.

zond-media, 2018-03-30:
is there any news on this proposal?

wernerdaehn, 2018-03-30:
Considering it heavily.
Problem 1: While forth mode would make the most sense, the RC sender has 3 position switches only. Hence best would be to request the limiter+endpoint mode and then use another switch to turn automatic travelling on/off.
Problem 2: When to turn off the automatic mode? Obviously when the switch is flipped, also when there is no more signal. Any other failsafes?
Problem 3: This will not be the only request. You could also record a movement and ask to repeat it over and over again. Or execute specific Point of Interest movements later. How to implement that so it suits future enhancements? More switches?? Certainly not.
Problem 4: Should we really start with this mode? How about starting with a record/playback mode for automatic movements?

What would be your take?

zond-media, 2018-03-30:
I think you greatly exaggerate the problem at this stage.
I agree with you, the best would be to request the limiter+endpoint mode and then use another switch to turn automatic travelling on/off (possibly Endpoint Button), but this mode must start with delay ~3-5sec and stop when the switch Endpoint Button is flipped OR when there is no more signal.
This is quite enough for RC !
To extend the functionality it is better to use the application for Android or iOS, but this is a completely different story..

wernerdaehn, 2018-03-30:
Okay, I can live with that.

Willyfan, 2018-03-31:
If you want, I can add these features in my android app. I need only to have a additional command set in order to set the automatic mode and start it.
For zond-media: you can download the app here:
http://william-fanelli.com/wp-content/uploads/myupload/ID_CablecamSetup_5.apk
Obviusly, no automatic mode is implemented for now... But I  have a lot of ideas for the app.
The problem is the bluetooth range, only some metres. not so much.

wernerdaehn, 2018-04-01:
I just found this BT module with 100m range
SparkFun Bluetooth Mate Gold

Trouble with turning on the automatic movement via the app is, how do you turn it off when the cablecam is out of range? Or in case of emergencies?
I would need add a timeout - if the app was not in range for longer than n seconds, stop immediately. I think I will do that.

zond-media, 2018-04-01:
Look at this lovely set, about 2 km range: [XRock 915MHz](https://www.aliexpress.com/item/wholesale-1set-XROCK-915MHz-500mw-Bluetooth-Box-V3-0-Radio-Telemetry-Modul-for-3DR-APM-PIX/32771355370.html) and [Internal shots](https://www.rcgroups.com/forums/showthread.php?2710802-XRock-915MHZ-500mW-Telemetry-Modules)

wernerdaehn, 2018-04-01:
I have used XBees in the past as well, equally nice as UART replacement. But they all need something attached to the tablet/phone, and that is the point I don't like.
BLE 5.0 might be the answer long term. Or Wifi?

zond-media, 2018-04-01:
What doesn't suit you in [this](https://www.aliexpress.com/item/wholesale-1set-XROCK-915MHz-500mw-Bluetooth-Box-V3-0-Radio-Telemetry-Modul-for-3DR-APM-PIX/32771355370.html) module? If I understand correctly, there is a Bluetooth bridge.

wernerdaehn, 2018-04-02:
I have tried it manually but not on the rope yet. So be very careful. There is one area of concern, that is that the cablecam never reaches the endpoint but stops right before it. This would break the automatic reverse.

Command: $j p 13
This is a new command and can be used to set all channel assignments one by one. Hence an alternative for $i. But while $i only supports the important commands, $j does all. In above example I want to set the p...Play function to channel 13 of the RC where a two position switch is assigned to.

In order for the Play button to be used, many conditions need to apply:
- Mode has to be the limiter+endpoints mode.
- endpoints have been set (are not the defaults +-MAX_INT16.
- RC sends a speed signal of zero. So using the RC you can always override the play temporarily.
- The Play signal is not older than 2 seconds. No problem for the RC as this sends it every n ms but when using the command $P 1 this is only valid for 2 seconds. Idea is, the app sends this command every second and if the connection breaks, the cablecam stops. Else the cablecam might drive into something and there is no way to stop it as the connection via bluetooth is broken.
- Of course in Operational mode, not endpoint programming

Note: It is absolutely fine to change the max speed/max accel while it runs by itself.

The implementation is to set the stick(!) to max_speed. If the endpoint is reached, wait for 5 seconds, then set the stick to -max_speed. As I change the stick values, it looks and feels to the controller as if you make those movements on the RC and hence the acceleration limiter, autobrake before the end points,... all is done.

cofhal, 2018-04-03:
How does the play option work?

wernerdaehn, 2018-04-03:
Isn't the post above clear enough? You assign a switch to a channel in the RC and tell the controller about that channel via $j p <channel#>
Then by flipping that switch, the cablecam starts to move automatically between the endpoints, assuming those had been set and you are in the correct operation modes.

Willyfan, 2018-04-04:
If I understood right: you can start automatic mode from RC with a new switch, or from the App with command $P 1 (this last way is to so clear...) but from the app I need to send the command every second or so or the cablecam stop. We can control speed in automatic mode with pots, or setting by the app, anyway automatic go to the max speed allowed. When the cablecam reach the end point stay in stop for 5 seconds.
I'm right?

wernerdaehn, 2018-04-04:
100% correct.

Willyfan, 2018-04-04:
There is a reason for not to add the automatic switch in tail to $i command? For my app this is the best (use $i instedad that $j), but if it is a problem I will review the layout, but is not easy to have backward compatibility.

wernerdaehn, 2018-04-04:
Usability mostly. Imagine you have a RC with 4 channels only and the ch#4 should be used for the last parameter in $i. You would need to type a lot of 256 numbers.
But actually, these people can use the $j command, nothing wrong with adding it to the $i command in addition. Will do.

wernerdaehn, 2018-04-04:
Done. $i now accepts one more parameter.

Willyfan, 2018-04-05:
Perfect. I'm really busy in this days, but I will try to find d some times for adding this changes to my app.
Have you a suggest in order to know the fw version?

cofhal, 2018-04-07:
The automatic mode works fine, with PWM, but with the VESC with the Serial port it does not work.

zond-media, 2018-04-13:
**wernerdaehn**, thank you so much for this work!
unfortunately I'm now busy until about the end of April..
I can carefully check only at the beginning of May and will write the result here.
keep it up!

wernerdaehn, 2018-04-22:
@Willyfan $V prints out the version string. Version string is a date in format YYYYMMDD.

Willyfan, 2018-04-23:
Ok, I'll modify  the app asap.

Willyfan, 2018-05-03:
I modified the app. It is a new version, for now this app don't work with old firmware.
www.william-fanelli.com/wp-content/uploads/myupload/ID_CablecamSetup_7.apk
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
zond-media, 2018-05-16:
When I push it by hand a bit more over the end point nothing happens at all...
I recorded a short video, so it will be easier to understand.
I show the work in Limit mode. Then I define the points. I switch to Limit mode with endpoints. I check in manual mode, everything is ok. I put the cart in the middle of the road and turn on the play mode. The cart moves to a point and stops. With my hands I move the cart through the end point. Then the other way. The cart returns to the point. The same thing happens with the help of the stick.
https://drive.google.com/open?id=1DSH0z6M5C4GuSWLpG9uP8EMHyu5dFhZq

wernerdaehn, 2018-05-16:
Got your point. It moves to one endpoint but never does reverse.
I'd like to check the $r again.
If you put the stick forward und read the position with $p, does the position value increase or decrease?
$r -1 means it does decrease.

You don't have to do that on the rope, you can simulate it by turning the sensor wheel manually. Just make sure you got the direction correctly. Check in what direction the drive wheel turns and then turn the sensor wheel in the (opposite) direction, as if it would be on the rope.

zond-media, 2018-05-16:
**wernerdaehn**, I did not read parameter $p, I immediately tried to change the reverse on the motor (esc - "Reverse", it was "Normal") and in the controller ($r = 1, it was "-1"), hung the cart on a rope and...  a miracle happened - it worked! ))

wernerdaehn, 2018-05-16:
Glad we looked into the proper direction.
I don't like the $r parameter either, tried in fact multiple things to live without but ended up with it being necessary.
Its function is clear, I assume. Somehow you drove over the end point. a stick movement further over the end point has to be prevented, reversing out of the overshot end point should be allowed. $r tells me what stick direction causes what drive direction.
I experimented with setting that automatically and actually it does, but there are limitations. For example I might push the stick forward a bit and the result is rolling downhill slowly. Only if the stick is moved a lot forward it drives uphill. At the end it was too dangerous for me.

zond-media, 2018-05-16:
well, we solved this problem. now, it would be great to store these points in memory so that when replacing the batteries, they do not have to re-define them.
p.s. not all commands are written in the Command Reference table, please correct ;)

Willyfan, 2018-05-16:
Dear all, I have a lot of work to do in these days but I will upgrade the app as soon as possible with command for auto mode.
Please let me know if someone tested it (the app), Anyway the last version is working ok for settings, on my cablecam.
A question for Werner: I see a update of firmware, what changes? What mean "Endpoint handling improved"? Thanks!

wernerdaehn, 2018-05-17:
Just the way it looks and feels, when the CableCam does stop. The brake distance was calculated and if the end point is in danger to be overshot, it does slow down. And if it really does overshoot, stop immediately.
As result it does slow down nicely and in the last centimeters the inertia drags it over the endpoint and therefore stops abruptly.
Now I have a range of 100 steps. The brake target point is 100 steps (20cm) before the end point and the motor has 20cm to stop smoothly. Only if that is not enough, it would overshoot the end point and stop asap.

zond-media, 2018-05-17:
**wernerdaehn**!
can you make it possible to save points in memory right after the endpoints are set?

Willyfan, 2018-05-17:
@zond-media: the points is saved in memory just now...

zond-media, 2018-05-17:
Are you sure?
I have zero points when turning on the power
They are only saved with the $w command, but this is not always convenient

Willyfan, 2018-05-17:
I will try again, but I remember that end point are saved. I don't know if something changed in the last firmware, I don't tried yet.

Willyfan, 2018-05-17:
...anyway, is very easy save it with my android app...

zond-media, 2018-05-17:
Oh sure!
but I would like to have such an opportunity with a minimum set of equipment.
Thank you for the app!

zond-media, 2018-05-17:
ok, thanks!

wernerdaehn, 2018-05-19:
Quite lengthy. I am closing this one. Feel free to create new issues in case I forgot an aspect.

Closed 2018-05-19.

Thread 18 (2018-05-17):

Writing Endpoints into the EEPROM right after are set

zond-media, 2018-05-17:
Add an opportunity writing Endpoints into the EEPROM right after are set

Willyfan, 2018-05-18:
Is a good Idea, in the firmware on the old card I modified for save in eeprom also the points just after setting.

Willyfan, 2018-05-19:
The 3 points are correct.
I remember this problem also with old board, and I modified the firmware in order to save position. Now is less necessary because you can save it with $w write in eeprom, but I used this feature many times before.
Sometimes, non only for swap batteries, that it live many hours. But I worked on a 3 days event, so at morning was very simple turn on cablecam in the same point and have all setting done.
I understand your worries about safety, but normally, in the real use, the cablecam is mounted on cable and turn on at one side, where you have easy access. So is not a problem remember it (and normally if 0 position change of 20 cm is not a problem).
If someone not remember the point he must reset the endpoints, but I think that this is not a normal case.
No difference if you save all settings or move in a separate position, but in my modify of your old firmware I save in separate position.
I think that other settings as acceleration don't need to be saved, because we have the control on RC, or by the app. The app, when you change some settings ask for save in eeprom when you close it if someone changed. For logical, I think that the better solution is take positions and setting separate.

zond-media, 2018-05-19:
Totally agree with you, @Willyfan
Additionally, I suggest adding the $P parameter. If it = 0 (default), the recording does not occur, if = 1 auto-record is enabled. Or, alternatively, add a button (maybe we can use Boot?) to store and load position.

> 1. Enter programming mode, set both endpoints, exit programming mode. Now I write the end positions into EEPROM.
> 2. You use the cablecam for a couple of hours and then swap the batteries.
> 3.  The point where you reconnect the batteries has to be the exact same point where you did that when starting the cablecam the first time, because that is where pos=0 is.

everything is correct, only my suggestion - add $P

wernerdaehn, 2018-05-19:
+1
But I don't understand the $P statement. You want it to "Play" automatically? That's the opposite of what I aim for - Play only when you can be sure all is setup and the user can exit at any time. Example: Lost connection with the RC for >2 seconds? Stop Play immediately.

zond-media, 2018-05-19:
Sorry, I forgot that $P it's for Play..
The letter is not important, let it be $z  ;)

wernerdaehn, 2018-05-19:
You mean a separate command in parallel to $w for writing just the positions?

zond-media, 2018-05-19:
No, I mean, it's a key to enable (=1) or disable (=0, default) write the end positions after exit programming mode.

wernerdaehn, 2018-05-19:
I can't find a reason why you would NOT want to store the end points. In my world last setting counts, hence saving the endpoints to eeprom always now.
Agree?

I have implemented it, currently testing it.

wernerdaehn, 2018-05-19:
Firmware uploaded.

zond-media, 2018-05-19:
> I can't find a reason why you would NOT want to store the end points

excellent, I agree, it will be good
I will test tomorrow and write the result here

Willyfan, 2018-05-19:
For who need a point zero different from actual access to cablecam, I suggest a command for reset to 0 only actual position. So, I can go in this point using pass trough mode and reset position.
Another useful command is a offset of end points. I added this in last firmware because sometimes when the pulley slip the actual position is not accurate and We need to offset to left or to right both end points during work.

zond-media, 2018-05-20:
Today I tested the new firmware. Excellent work, thank you @wernerdaehn !
There was a problem with braking at high speeds. Can you add a parameter to adjust the brake stages? At high speeds, I need to brake much earlier than at slow speed. It would be great to have such  possibility of adjustment.
p.s. command $A still doesn't work..

wernerdaehn, 2018-05-20:
Can you show me what high speed braking looks like in your case?
You are using a RC car ESC, not the VESC, are you? I recall that from the last video but want to make sure.

In theory the controller calculates the brake distance at any time and if there is the danger to overshoot the endpoint, it reduces the stick signal in a linear fashion. With the VESC the stick translates directly to a speed and hence the speed is reduced nicely.
With a car ESC you cannot control the speed, only the energy level plus the amount of slow down is programmed as drag brake into the ESC.
What might happen now is that the drag brake is not enough at high speeds, the brake distance calculation figures it will stop beyond the end point plus the max error distance ($g) and hence go into an emergency brake, meaning setting the output signal to neutral. If this brake is way more powerful then the drag brake when reducing the stick signal, the speed might drop so the end point is no longer overshot significantly and continue with the normal braking. Result is an uneven braking.
You can test that theory by setting $g to something significantly higher. Just keep in mind that the end point might now be overshot by a greater degree and allow for that when setting the end points.
Sooner or later I would recommend using the VESC.

wernerdaehn, 2018-05-20:
As said, you don't have to reduce the speed by hand.

The controller know the speed of the cablecam. It has a maximum acceleration defined.
Hence it can calculate the brake distance and if that is so high it is over the endpoint, the speed signal is reduced linear.
Example in metric units:
Speed = 10m/s
Accel = 1m/s²
Hence it does reduce the stick from the current position (say 50%) to zero in 10 seconds (=speed/accel). It would reduce the stick signal by 5% per second.

If the stick is 10% and the speed = 1m/s, it would reduce the stick by 10% per second.

Give it a try. Set the acceleration to a very low value. You will see it does start breaking really early and the faster you go the earlier it brakes. Just as above example with 10m/s and 1m/s has shown.

zond-media, 2018-05-20:
I understand, thanks for the detailed explanation of the algorithm of work and for your time! perhaps you can close this issue ;)

Willyfan, 2018-05-21:
I have a question for Werner related to the algorhitm above: As you say (and I'm agree) with normal (car) ESC you can't control the speed by input but only energy.
But as you know the real speed of the cablecam (from cablecam sensor input) what is the difference from this ESC and VESC? I mean, the controller can manage energy in order to have desidered speed. Or not?
I understand that VESC is better when you need to take braked the cablecam on a slope cable, But car ESC have a lot more power, also 120-150 A vs 80A max for VESC.
Perfect ESC will be a VESC with more power.....

wernerdaehn, 2018-05-21:
My initial goal was to use a PID control loop in the cablecam controller that sets the power according to the sensor wheel. I mean, everything is there. Sensor wheel says the speed is too low, hence the PID controller does increase the power signal for the ESC and vice versa.
Generally speaking that worked okay. But not good enough.
- Problem 1: While you can increase the ESC signal to go faster, decreasing the signal does not engage a proportional brake. The ESC did either slow down the motor based on the drag brake value or the full brake if the speed signal is neutral. You cannot control the brake to the same level you can control speeding up.
- Problem 2: The resolution was not high enough. At neutral you expect the cablecam to stand still. In reality it did move around the target point.
- Problem 3: Low speed movements near neutral. One thing you have to do is eliminating the neutral area of the ESC. So if the ESC has 1500us+-30, the controller should not output 1520, the value should jump directly to 1530 or 1470. No problem if setup correctly. But even a signal of 1550 would not mean necessarily a motor movement. It would power the motor a bit, you can hear it, but the power is not enough to actually turn the motor. Such non-linear behavior does not work well with a PID controller.
- Problem 4: The PID values change constantly. Different camera, different hill steepness, tension of the rope.... you had to spend a lot of time to tune in the parameters and the next time different ones were needed.
- Problem 5: For proper resolution at low speeds you had to program a throttle curve. Only then you can control the low speeds and reach the top speed. Again, a non-linearity the PID logic cannot cope well with. Worse, all ESC I tried did use the throttle curve on the forward side only. In reverse the throttle was linear.

So at the end it did work at slow to high speeds. But did not work for very slow speeds and standstill.
Two videos that show that it did work in general. But because I was never satisfied I removed that code when the VESC turned out to be so much better and none of the RC vendors were willing to implement a speed mode in their ESC.
https://www.youtube.com/watch?v=yxlcmSTsAeA
https://www.youtube.com/watch?v=SgqjXSWjWp0

wernerdaehn, 2018-05-21:
@zond-media Regarding $A:
I removed that command, it is now
     $j a 14
This would map the aux output to whatever input channel #14 provides. See $i to validate the input and the servo1&2 outputs.

zond-media, 2018-05-21:
Ok, thanks!

wernerdaehn, 2018-05-24:
implemented

Closed 2018-05-24.

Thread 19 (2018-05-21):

How accurate is the position reading?

wernerdaehn, 2018-05-21:
Can you please keep an eye on the position sensor?
In my case I marked one magnet of the sensor wheel with a pen and hence know the exact position. And I marked the rope at position 0.
When I drive back and forth, high & low speeds, high & low accelerations, the point does not move at all. Always use the $p command to get the position. Just saying it does not stop at the end point precisely has too many other variables. Mass of the cablecam, brake momentum etc.

I had to tweak the STM encoder settings a bit but now I believe it works perfectly for me. No slippage as the sensor wheel can move freely and is pressed via the rope tension into the rope. And no hall signals get lost.

There could be a couple of reasons why you results might be less accurate and I want to get a feel how well all works at the moment.
- Magnets induce a magnetic field in the alloy causing the hall sensors to trigger.
- The distance between the hall sensors in relation to the magnets is not optimal. I have 8mm between magnets, 13mm between the two hall sensors. Keep in mind, there is a hysteresis in the hall sensors and the direction is derived from the fact which flank fires first - sensor1 or sensor2. Currently I believe 8mm/8mm would have been better given that we alternate the magnets north/south and the hall sensor fires on north only.
- Capacitors near the hall sensors needed or not? I do not use any at the moment.

zond-media, 2018-05-22:
@wernerdaehn, I tested the latest firmware version. works terribly. does not correctly record end points after battery replacement. flies the endpoints even further than the previous firmware.
return it as it was, please ;)

wernerdaehn, 2018-05-22:
It should not be more than 44 steps more than before (I sensor wheel revolution). Is it about that distance or way more?

What do you mean with "does not correctly record end points after battery replacement"?
And for $r, you have programmed it or just read it? What is the value before you set the endpoints? (Because if $r=0 then the end point programming tries to guess it)

wernerdaehn, 2018-05-22:
I have made the changes but not tested them. Not sure when I can test but feel free to give it a try.

wernerdaehn, 2018-05-22:
If you just read $r, then please program it as well. $r 1 and $w.
In the firmware of today I test if $r = 0 and program it together with the end points.

zond-media, 2018-05-22:
Thanks! I will test in the first half of the day tomorrow and write the result. about the command $r 1 understood, I will do as you write

zond-media, 2018-05-23:
Need ftdi module support like this [http://rctimer.com/?product-834.html](url) on rx3-tx3 pin. Can you do that?

wernerdaehn, 2018-05-23:
Simple UART, so why not.
The original CC3D Revo has a 433MHz module onboard as well. It is connected via SPI and I did like Bluetooth better (because then I don't need a receiver for the tablet). But I can enable that as well, if you like. Just a thought.

zond-media, 2018-05-23:
Perhaps the best solution would be to buy this module  http://rctimer.com/?product-834.html ?

wernerdaehn, 2018-05-23:
Yes, it is cheaper and works out of the box. Only thing I don't like is that it is yet another PCB just like today I use the bluetooth module. With the original CC3D Revo the 433 Module would be onboard already.
I just looked for a CC3D with onboard OPLink and did not find any in Europe, though.

zond-media, 2018-05-23:
I’m just now upload new firmware. Nothing has changed...

wernerdaehn, 2018-05-23:
Video please. Showing where you program the start point, how it brakes there, what happens when you run the play command, what happens to the start point when you restart the cablecam. Okay?

zond-media, 2018-05-23:
Strangely, now the position is saved and loaded correctly, but the move for the end points is still great. In the photo I showed the installation of the end points at a distance of about 6 meters. https://drive.google.com/file/d/1n0BcQoQk7_kxnT1lFSauiGHxpjp1nHZ0/view?usp=sharing
https://drive.google.com/file/d/1EBWfAJsX7KWBaN2xs0utcCGs9_Ifmju2/view?usp=sharing
https://drive.google.com/file/d/1Ek4Lk84NlM8VU_OAN6_rcWTKZwFNlvDa/view?usp=sharing

wernerdaehn, 2018-05-23:
I think I know what is going on. It is not so much related to the firmware of last weekend but a few days before that.

Please set $g 10 and save it. That causes the ESC to brake more aggressively and not just once the endpoint has been overshot.
NOTE: $g 0 disables it, so that's no good.

The controller can output 2 kinds of values via PPM: Slowly reduce the thrust or neutral.
When you listen to the motor, it makes a different noise when passing the endpoint. It brakes heavily once the end point has been overshot but none of that noise is heard before reaching the endpoint. It rather looks like free wheeling while getting closer and closer to the end point.

And that makes sense:
- When the brake distance based on the current speed is calculated to be slightly over the end point, the controller does reduce the speed signal. In your case it does slow down but not enough to stop near the end point.
- When the cablecam passed the endpoint, a failsafe is triggered. Now I don't care about the speed but set the output to neutral. For your ESC that is the signal to brake as hard as possible with the drag brake.
- When the brake distance calculation already shows the endpoint will be overshot significantly, I put the output to neutral as well. That is the emergency brake. Idea is, if the speed = 100 and the brake distance is 5000 steps beyond the end point, it is better to brake as hard as possible now already.

The change affecting you is the last one. The emergency brake $g distance defaults to 100. Which is quite a lot in absolute terms. But on the other hand, at very high speeds, the brake distance might easily be 100 steps higher for a few milliseconds. The VESC does not like getting speed = 0 every few seconds and it is not necessary either. Therefore I have added a speed component into the emergency distance. At speeds close to 0 the emergency brake kicks in at 100 steps position. The higher the speed is, the higher the emergency brake distance gets.
With your controller an occasional neutral signal to engage the brake is actually desired.

    if (activesettings.max_position_error != 0.0f && (pos + brakedistance >= semipermanentsettings.pos_end + activesettings.max_position_error + 30.0f*brakedistance/activesettings.max_position_error))
    {
      controllerstatus.emergencybrake = true;

wernerdaehn, 2018-05-23:
Stupid me, the lower the value for the max_position_error is the smaller the last component in the if condition should be. Which is not the case. Let me change that quickly.....

wernerdaehn, 2018-05-23:
Updated Firmware uploaded.

zond-media, 2018-05-23:
Now, what I need! Thank you!
Add support for the FTDI module and the system will be fully ready for work!

wernerdaehn, 2018-05-23:
As said, the FTDI module will work already. Just need to configure it for 38400 Baud and connect it.

(Note: I will delete all these posts here in the next days as the actual intention of this github issue is to capture position sensor reading issues.)

zond-media, 2018-05-23:
How can I configure for 38400 ??

zond-media, 2018-05-23:
I'll try with PuTTY, but then I try to click on keyboard, no answer from controller

zond-media, 2018-05-23:
Ok, I'll configure to 38400 with 3DRRadio, but  in terminal I can't connect..

wernerdaehn, 2018-05-23:
Or the Air Radio Config tool as it says at the bottom of the product page you linked?
http://rctimer.com/?product-834.html

zond-media, 2018-05-23:
I did it. speed 38400, but nothing happens when I press keys in the terminal window

wernerdaehn, 2018-05-23:
Best would be to diagnose it without the cablecam controller in the picture. Connect the module working in the cablecam to you PC, with the 38400 baud rate and the ground station module as well. Since this is supposed to be a transparent link, every character you send in the one putty terminal should appear in the other and vice versa.
Only when that works it makes sense to even look into the cablecam controller.

Agreed?

zond-media, 2018-05-23:
Because on Aux ch. I have digital servo with other neutral point

wernerdaehn, 2018-05-23:
??? A servo that has center not at 1500??? Never seen that. Unless somebody reprogrammed the servo - which is possible with some digital servos.
I would really like to avoid that. Do you insist?

zond-media, 2018-05-23:
I would be very very grateful if you do this!

wernerdaehn, 2018-05-23:
Done. See $A.

zond-media, 2018-05-23:
Thanks a lot! Tomorrow I’ll check it

zond-media, 2018-05-24:
Everything is working as I wanted, amazing accuracy at any speed. I was able to set the neutral point for the servo (= 1474). It is very cool! Thanks again for the excellent work! I hope for long-term cooperation!

Closed 2018-05-24.

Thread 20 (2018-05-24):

How accurate is the position reading?

wernerdaehn, 2018-05-24:
Can you please keep an eye on the position sensor?
In my case I marked one magnet of the sensor wheel with a pen and hence know the exact position. And I marked the rope at position 0.
When I drive back and forth, high & low speeds, high & low accelerations, the point does not move at all. Always use the $p command to get the position. Just saying it does not stop at the end point precisely has too many other variables. Mass of the cablecam, brake momentum etc.

I had to tweak the STM encoder settings a bit but now I believe it works perfectly for me. No slippage as the sensor wheel can move freely and is pressed via the rope tension into the rope. And no hall signals get lost.

There could be a couple of reasons why you results might be less accurate and I want to get a feel how well all works at the moment.
- Magnets induce a magnetic field in the alloy causing the hall sensors to trigger.
- The distance between the hall sensors in relation to the magnets is not optimal. I have 8mm between magnets, 13mm between the two hall sensors. Keep in mind, there is a hysteresis in the hall sensors and the direction is derived from the fact which flank fires first - sensor1 or sensor2. Currently I believe 8mm/8mm would have been better given that we alternate the magnets north/south and the hall sensor fires on north only.
- Capacitors near the hall sensors needed or not? I do not use any at the moment.

Willyfan, 2018-06-13:
Hi Werner, I'm waiting for a VESC in order to try also this issue.
If you are interested, ther is a guy that sell clone of vesc 6, at around 130 pouds. You can fint him here: http://www.electric-skateboard.builders/t/hw6-4-based-esc-escape/37579/60

Willyfan, 2018-07-02:
I checked the precision of the sensor, and it is perfect. I have sometimes some problem because a little slip of the wheels when accelerate too quick. bu the sensor is ok, and beside mi wheels are in derlin. I will try putting some rubber o-ring on the wheel in order to eliminate the little slipping.
I'm using a old circuit for sensor, with 3.3 volts regulator and it work good. I have now some boards without voltage regulator, I will try it also.

DmitriySurin, 2018-07-27:
I spent two weeks to figure out the algorithm of the hall sensors step. Here it is: 1, 1+2, 2, 0. I missed 1+2 step in my configuration hence nothing works. Could you explaim more about 8/8 mm does mean in your guide above?

wernerdaehn, 2018-07-27:
Check the bottom of this page:
https://github.com/wernerdaehn/CC3D-CableCam-Controller/blob/master/Step%206%20-%20Connecting%20the%20Position%20Sensor.md

The point is not that N/S poles are 8mm apart and so is the sensor, it should be 8mm to 13mm for example.
There are two effect:
1. When one sensor fires on rising/falling flank, the other sensor is read. This determines the direction. To make things more obvious, the goal is that first sensor1 gets a rising flank and then sensor2. Then sensor1 gets a falling flank, then sensor2. And in the reverse direction, it should be sensor2 first and sensor one after.
1. There is a hysteresis, so the sensor switches later once the north pole is in reach and switches later when the north pole gets out of reach.

In other words, when turning the sensor wheel with a constant speed, there should be a pronounced time gab between leading sensor On and trailing sensor On. Is there?

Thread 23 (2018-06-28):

Passthrough and speed limit

Willyfan, 2018-06-28:
Dear Werner,  yesterday night I noticed during some test on the board that the **passthrough mode** is influenced from max speed control pot, but not from acceleration pot.
If I switch to **Passthrough with speed limits** all 2 pots works (and it is correct).
Also exponential factor change the response of Passthrough mode.
I remember that before this mode was input=output without filters.
It's a choice or it's an error? Also, is not a big problem as we can set max speed to 1 and take pot at max for test, but just to know.

wernerdaehn, 2018-06-28:
That would definitely be an error. If passthrough & operational (no endpoint programming) is set, then input=output.
The only calculation is done via the $n (input) $N (output) value ranges.

Willyfan, 2018-06-28:
About range is logical because you need to "translate" sbus in pwm.
But I'm sure that in passthrough & operational the speed pot work. I noticed because I forgot the pot at min, and motor start very slowly. Turning pot at max all work.
Acceleration pot don't have influence in this mode.

A question not related with this problem: I seen just some minutes ago in some your images that you have connected a yellow wire to CH6/TX6 pin on the board. What is? If I understand correctly, VESC is connected to Servo 3 & 4 - but this board have some different layout, so I ask...

wernerdaehn, 2018-06-28:
Okay, should be easy to check and reproduce for me. Keep you posted.

This is the Gimbal Output connected via an external SBus inverter to the Ronin.
see last line in
https://github.com/wernerdaehn/CC3D-CableCam-Controller/blob/master/Implementation.md#hardware-mapping

I plan to add individual pages for the hardware connections soon.

wernerdaehn, 2018-07-22:
Hmmm. Yes, you are obviously correct. In passthrough mode the speed poti does change the speed.
The question is, is that good or bad.

Purely from the implemented logic speaking, if there is an output range configured, say +-700us, then 100% forward should be a pulse 1500us+700us (neutral plus max).
The speed poti does change the max allowed value. So a poti of 50% reduces above example the max value to +-350us.

If you remember, initially we said the poti controls the stick movement. The result was that a speed limit of 10% did ignore all stick movements in the range of 10%-100%. Instead we changed it to:
The stick should use the full range and we scale the output. And that we do, we scale the output.

Changing that is simple, I just need to add another if-then-else when generating the output. If passhrough then scale based on the ESC output, when limiter is on then scale based on the speed limiter.

Question is, what is better? Currently I am for adding that. Other opinions?

Willyfan, 2018-07-24:
I think that the user expects that passtrough mode is a input output direct mode. In the real life, there is no reason for use passtrough mode, except when you test or check the system.
If you want only ignore the endpoints, passtrough with limits is perfect.
So, in my opinion is better that poti don't work in this mode,  if is not a problem. We will see other opinion anyway.

Closed 2018-09-22.

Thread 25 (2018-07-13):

Validate that the defaults are used after first time flashing

wernerdaehn, 2018-07-13:
We had a case where the defaults were not used and all was set to <nan> or 0.

wernerdaehn, 2018-07-20:
Thanks. I don't understand why that happens at the moment but will fix it this weekend.

wernerdaehn, 2018-07-22:
Should work now.

Closed 2018-07-22.

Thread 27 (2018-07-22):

Bluetooth connection FLIP 32 and HC-06

DmitriySurin, 2018-07-22:
I have HC-06 manually programmed to:
AT
OK
AT+UART
+UART:38400,0,0
OK
AT+NAME
+NAME:cablecam
OK
AT+PSWD
+PIN:"1234"
OK
AT+VERSION
VERSION:3.0-20170609
OK

But it doesnt work for FLIP.

wernerdaehn, 2018-07-22:
That +UART:38400,0,0 worries me.
Can you change the settings to UART 38400,1,0? It should have no parity, one stop bit.

DmitriySurin, 2018-07-22:
No it doesnt help

wernerdaehn, 2018-07-28:
I have uploaded a firmware version with debugging support for the bluetooth UART.
- Connect the board to USB, open the terminal.
- Connect the bluetooth module.
- Via the USB terminal execute the command $d b. This turns on debugging. From now on, whenever the bluetooth module does send a char to the controller, this char is also printed in the USB terminal. In my example I send via my tablet the text abcd to the bluetooth module and on the USB terminal abcd gets printed.
- In the USB terminal execute $d B after you sent data via bluetooth. This command shows the lowest level error codes on UART3. Frame error, parity error, overflows, noise.

As said, this for monitoring the RX pin on the UART3 of the controller.

I hope this helps us isolating the issue.

DmitriySurin, 2018-07-30:
I send 123456 via Serial bluetooth terminal and I can see very strange result in your debugging mode:

Bluetooth debug: ON
▒▒▒▒

DmitriySurin, 2018-07-30:
Also $d B said:

Bluetooth UART's last error code flag says: no errors

wernerdaehn, 2018-07-31:
That does not make sense. Sending different characters resulting in the same target character without frame or parity error is impossible. Something is wrong.
What I would do next is connect the PC via a USB-to-UART adapter to the cablecam controller's bluetooth pins (without 5V) and proof the UART is fine or not.

DmitriySurin, 2018-07-31:
What I would expect to see in terminal? At? Or what?

wernerdaehn, 2018-07-31:
If you send "123456" to the UART, in the USB terminal you would see "123456".

I have added a print statement into the UART3 receiver logic. Before the received char is put into the UART buffer, it is also sent to the USB terminal.

            void UARTX_IRQHandler(UART_HandleTypeDef *huart) {
                if (controllerstatus.bluetooth_passthrough) {
                    PrintSerial_char(byteReceived, EndPoint_USB);
                }
                huart->pRxBuffPtr[huart->RxXferCount % huart->RxXferSize] = byteReceived;
                huart->RxXferCount++;
            }

DmitriySurin, 2018-08-01:
Ok. I cheked it. Thats works. Flips UART is fine!

DmitriySurin, 2018-08-06:
I bought HC-05, and now everything is work fine.

Closed 2018-09-11.

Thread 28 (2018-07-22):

Powering the FLIP board via 6v BEC.

DmitriySurin, 2018-07-22:
My ESC is SKYRC 160. Built-in 6V/3A BEC. Is this OK for FLIP F32 board and signal from hall sensors?

wernerdaehn, 2018-07-22:
Yes, no problem. Just connect the ESC to the Servo1 connector with all three pins, signal, +5V and GND. The Flip has a power converter built in to deal with every normal BEC voltage from 5V to 7V.

Closed 2018-07-27.

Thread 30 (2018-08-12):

Deceleration problem

Willyfan, 2018-08-12:
During some test on the rope, I found a little problem with deceleration near to the end points. I see this in autoplay, but it is the same if you drive the cablecam to end points at max speed.
The problem is that the deceleration is not smooth, but a bit "choppy".
I solved the problem rising the max allowed error parameters from 100 (default) to 300.
Now the deceleration is smooth, but when the cablecam arrive to the end point speed is not zero (anyway is NEAR to zero) and it stop abruptly.
My mind is that the calculation for deceleration have some kind of error, so, if allowed error is low the board try to adjust speed creating the "choppy" deceleration. When max error is higher, The deceleration go until the cablecam don't is on the end point, but because this error speed is not zero, so the board brake in order to don't go over the end point.
My guess is that deceleration start too late, Or is less that we need. Maybe also cablecam inertia do something, anyway, is not possible to have a parameter for "anticipate" a bit the deceleration? Just for debug...

wernerdaehn, 2018-08-13:
We need to separate here between VESC and RC ESC. With the RC ESC there is not much I can do. I can put the stick slowly towards neutral - little brake force - or put it in idle - strong brake force. There is no _proportional brake_ in forward/reverse mode. Hence the best is a narrow max-pos-error of 100 to switch between both brake modes more often.

With the VESC we have conflicting requirements. We want to stop at the end point, we want not to drive over the end point and we don't know the inertia of the cablecam. (Also the inertia is not static - driving up/downhill, rope tension etc). I have tried multiple things like setting the end point 100 step early and drive at low speed to the very end. Nothing really did work well.

Which of the two modes are we talking about and what is the suggestion? Also a video would be nice to agree it is the above or something that can be optimized.

Willyfan, 2018-08-13:
I'm using vesc and not rc esc.
I have a video on my phone. I'll publish it in the afternoon, but on video is not so clear what I mean.

DmitriySurin, 2018-08-13:
And I am using esc from skyrc. From my side I can say that long acceleration and decceleration affect more choppy brake. Like abs on the car. When I put low accell and deccel value my cablecam sleep on the rope at high speed while braking but there is no choppy effect discribed above. My suggestion to separate accel and deccel value for manual mode and for automatic braking near end points. Also it would be nice if we could independently adjust accel and deccel value.

DmitriySurin, 2018-08-13:
Hence the best is a narrow max-pos-error of 100 to switch between both brake modes more often. What does it mean? In my cablecam construction there is big gear ratio and I am using 4-6s battery. So from the esc side the drug brake is strong enaphf to hold the cablecam via big gear ratio.

Willyfan, 2018-08-13:
This is a video where you can see that the Cablecam brake an go during deceleration. As you can see, the Cablecam jump slightly near to the end point.
No problem with accelleration.
The video is with max error at default value 100.
Raising at 300 (or more) the deceleration is always smooth, but when the camera is at the endpoint speed is not zero, so it brake abruptly.
This is not a big problem, but if is possible reach speed zero without this effect (also if the camera went slightly over the endpoint, all is better.

Anyway, is better the results with hight max error value than the choppy deceleration, for quality of video.

wernerdaehn, 2018-08-14:
What are the drag brake and initial brake settings on the ESC itself? Rather high values or low?

Imagine the following situation:
CableCam is 5m away from the endpoint and according to the accel settings it has to brake now.
In the next cycle it is 4m away and the speed has not been reduced significantly. The brake distance calculation shows it will overshoot the end point by 1m. As you see, moving the stick slowly to neutral does not cause the cablecam to brake enough. What signal should I send to the ESC?

A few cycles later, it is exactly at the endpoint but has some excess speed left. It will overshoot the endpoint by 1m. What should I send to the ESC?

Willyfan, 2018-08-14:
> What are the drag brake and initial brake settings on the ESC itself? Rather high values or low?
I'm using a VESC6, so I don't set drag brake and initial brake.
Now, I tested the cablecam far from end point. If I move the stick at center, the cablecam  decelerate very smooth and stop (after I released the stick). But I guess that this is a combination from deceleration and camera inertia, and I can't know how much distance the camera stop from where I released the stick. There is a difference from teorical distance based only on deceleration and true distance.
A good results near to end point should be the same, move the stick at center (stop) just in time for stop the camera on  the end point. Maybe with a corrector parameter?

Willyfan, 2018-08-14:
About vesc6 I opened a issue about configuration some days ago. Maybe I'm using vesc6 in wrong way. I set it in FOC, How do you set your VESC?

DmitriySurin, 2018-08-14:
I use high values for brake. Also I can very smooth stop my cablecam manually moving slow the stick to neutral. Also the braking distance from what I can during my tests not longer than at operational mode. So the main question for me why under the same condition the result is too different?

DmitriySurin, 2018-08-14:
Also I dont understand how the cable cam can know the speed if the diameter of the halls wheel and the distance between the magnets can be so different from cable cam to cablecam? What is the frequency of calculation the braking distance? One hall step or what?

Willyfan, 2018-08-14:
@DmitriySurin
The cablecam don't know the absolute speed in m/s, but at pulse/second. As also distance in measured in pulse and not metres, it's ok

wernerdaehn, 2018-08-14:
@Willyfan  Okay, will document my settings on the VESC next weekend.

@DmitriySurin The statement "I can smoothly stop my cablecam manually moving the stick to neutral" is not a fair comparison. The controller does not let the motor slow down with its settings but by the programmed acceleration value. A fair comparison would be you want to stop the motor faster than with drag brake alone, hence you have to put the stick in neutral once a while. This would obviously not be as smooth as the drag brake alone.
I'd like to proof that by you setting a lower acceleration value in the controller. This should then never kick in the emergency brake.
What I wonder about is the slow speeds and slow accel I see in your video. I hope it is not something else. Do you have bluetooth working menawhile? Would be interesting to see the emergency brake output during the drive.
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
wernerdaehn, 2018-08-22:
I can't see the problem on my bench test. Can you please try with the firmware I just uploaded. I have added better output when using $d P.

Willyfan, 2018-08-22:
please give me one hour and I send you a log.

Willyfan, 2018-08-22:
Ok, updated firmware and tried.
the logs (always at erpm max 10000, and in manual mode, not autoplay).
I done some test without gimbal, and some test with additional weight of gimbal.
No gimbal, to left direction
```
Startpoint brake on. pos-brakedistance= -47663.000 - 563.947 = -48226.945 < -48220.000, braking distance= abs( -0.990[%] ) / 0.507[%/s] * 571.429[steps/s] / 2 = 563.947
Startpoint brake on. pos-brakedistance= -47736.000 - 563.947 = -48299.945 < -48220.000, braking distance= abs( -0.980[%] ) / 0.507[%/s] * 571.429[steps/s] / 2 = 563.947
Startpoint emergency brake on. pos-brakedistance= -47762.000 - 558.233 = -48320.234 < -48220.000, braking distance= abs( -0.970[%] ) / 0.507[%/s] * 571.429[steps/s] / 2 = 558.233
```
no gimbal to right direction:
```
Endpoint brake on. pos+brakedistance= -47177.000 + 563.947 = -46613.055 > -46625.000, braking distance= abs( 0.990[%] ) / 0.507[%/s] * 571.429[steps/s] / 2 = 563.947
Endpoint brake on. pos+brakedistance= -47117.000 + 563.947 = -46553.055 > -46625.000, braking distance= abs( 0.990[%] ) / 0.507[%/s] * 571.429[steps/s] / 2 = 563.947
Endpoint emergency brake on. pos+brakedistance= -47081.000 + 558.233 = -46522.766 > -46625.000, braking distance= abs( 0.970[%] ) / 0.507[%/s] * 571.429[steps/s] / 2 = 558.233
```
with gimbal left direction:
```
Startpoint brake on. pos-brakedistance= -47667.000 - 563.947 = -48230.945 < -48220.000, braking distance= abs( -0.990[%] ) / 0.507[%/s] * 571.429[steps/s] / 2 = 563.947
Startpoint emergency brake on. pos-brakedistance= -47823.000 - 501.090 = -48324.090 < -48220.000, braking distance= abs( -0.868[%] ) / 0.507[%/s] * 571.429[steps/s] / 2 = 501.090
```
with gimbal right direction:
```
Endpoint brake on. pos+brakedistance= -47186.000 + 563.947 = -46622.055 > -46625.000, braking distance= abs( 0.990[%] ) / 0.507[%/s] * 571.429[steps/s] / 2 = 563.947
Endpoint brake on. pos+brakedistance= -47123.000 + 558.233 = -46564.766 > -46625.000, braking distance= abs( 0.970[%] ) / 0.507[%/s] * 571.429[steps/s] / 2 = 558.233
Endpoint emergency brake on. pos+brakedistance= -47048.000 + 529.661 = -46518.340 > -46625.000, braking distance= abs( 0.919[%] ) / 0.507[%/s] * 571.429[steps/s] / 2 = 529.661
```
In every test I can see the intervention of the emergency brake (also for the "sound" of motor).
As usual, I also test to release the stick in the mid of rope, and camera stop smoothly in around 2 seconds and maybe 3 metres.

Willyfan, 2018-08-22:
The strange thing is that speed is **always** 571.429 step/s. There is something wrong in this.

wernerdaehn, 2018-08-22:
Please reduce the accel significantly and also $d P so we can see the intermediate values.

While you are driving the output of $p would be interesting as well as I print out the two speeds, based on the interrupt and based on the pos difference. Maybe that gives an indication if the speed is correct or not and which.

It can be that the speed remains the same. As the speed is primarily the time between two hall pulses (rising flank), if there is no hall puls, the value is not updated. And after 2 seconds I assume a speed=0. Can't see why it should remain 571 for more than two cycles but....

Willyfan, 2018-08-22:
I suspect that from bluetooth terminal the command $d P don't work. I try to put command with putty, and I don't switch off the board.

wernerdaehn, 2018-08-22:
Also, this might be too much text for the bluetooth connection...

wernerdaehn, 2018-08-22:
I definitiely don't like the speed reading. Let me revert that back to pos-difference only.

Regarding the "you don't start at zero" we need to keep an eye out. There should not be a difference to before. I certainly don't store the current position anywhere. The only thing that can change the position is when switching $r. Because then the current position is inverted.
I'll upload the revised code in a minute.

Willyfan, 2018-08-22:
Ok.
Now is raining a lot, so i can do test as it finish...
Anyway, as yopu can see, the position is not more from zero and value around it (before I had from 0 to 1700) but is at -650000 or so. I don't know what happen.

IMPORTANT NOTE: as my rope is not so long, the deceleration start before that the camera was at max speed, or, to say better, before that stick arrive to 100%. In both cases, the stick is around 0.650 when endpoint brake start. But there is an inconsistence: when brake start, the calculated brake distance is around 540, in both
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

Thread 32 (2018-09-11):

Buzzer for end points.

DmitriySurin, 2018-09-11:
Is it possible to use buzzer outputs of the flip board  as the confirmation of setting the endpoints? One beep for the first and two beeps for the second endpoint? Also it be useful to dyplicate onboard mode light via led strip output.

DmitriySurin, 2018-09-21:
Any idea?)

wernerdaehn, 2018-09-22:
Implementation is probably simple. Need to find a spare GPIO pin, PWM output and we are good.
But is it worth it? You would need to attach a buzzer. For this one use case. Often you want to be as quite as possible. and you get the same output if you would use a bluetooth connection plus more.

What would be your arguments offsetting this?

DmitriySurin, 2018-09-22:
The arguments is very strong...Carrying a 30 000 USD camera onboard I want be for 100 sure thats my endpoints are set propertly by any reason. Any operation should have the feedback from the device. Flip board have separate buzzer outs.

wernerdaehn, 2018-09-23:
That's an argument for getting feedback. But not if bluetooth or buzzer, is it? Yes, the pins are not used at the moment.

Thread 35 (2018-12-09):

odriverobotics.com support

wernerdaehn, 2018-12-09:
Status update:
I can read and control the odrive's velocity mode now. Similar to the VESC.
Need some more testing but then I can release the new build.

Willyfan, 2018-12-18:
I must rebuild a cablecam in order to test this solution. I seen that the odrive controller is available now (but only in USA and not in europe for now), so I will order one of this at begin of next year.
As I have many AS 5047 encoder with a custom designed board, I will try with this encoder instad the amt 102. I hope that this is ok. When you are ready, I want ask you what do you think about position encoder, If we need our encoder or the motor encoder is good.

wernerdaehn, 2018-12-18:
I don't know the effects of slippage. And I expect it to be dependent on many external factors. A heavy rig on a steep hill and aggressive driving and running for a long time will have pronounced slippage. For sure.
The opposite of above extreme situation might be okay.

But frankly, it does not matter for the Controller. We have two position value sources, motor controller (VESC or oDrive) or running wheel. You can switch to either one. It does matter for you of course because you need to decide if the hardware needs that or not.

The perfect solution would be to have both and the running wheel has an encoder as well. I am just struggling to find a mounting solution that is easy enough for the majority of the people.

Willyfan, 2018-12-19:
If you remember, some times ago I request for a "goto" feautures. You suggest to use the odriverobotics controller because it have this features but I guess that it work only with the encoder on the motor.
We can use both as you suggest but maybe need to be inplemented in the controller in this case.

Willyfan, 2024-06-05:
Hi Werner, it's many time that I dont see you in this page...
I have only a little question: some message above, you speak about use VESC (or oDrive) as position sources. It's possible now or maybe we need to write some code for it?

wernerdaehn, 2024-06-05:
There are three things to consider.

1. Do we send position commands to the ESC (or thrust or speed)?
2. Where do we get the actual position from?
3. What if it should hold the current position?

The problem is, all of these three questions are in flux. It depends on the current capabilities of the ESC.

Ideally, we would sent the ESC constantly the desired position and the ESC drives towards that or holds the position. The actual current position comes from an encoder on one of the other wheels as the driven wheel has slippage.
Hence it would be good if the ESC has that encoder connected and when sending the desired position, it is based on this encoder's position.
Third, the motor encoder should be a relative type, meaning it reports the angle. The position encoder should be a hardware absolute encoder ideally.

For the VESC I have no hope any of this will get implemented. For the ODrive they were moving slowly into that direction but I did not check the state for a long time.

Hence this code should be considered as work in progress.

Willyfan, 2024-06-06:
Dear Werner, I not found instruction about oDrive  connection. It is connected just like vesc? How configure firmware for using oDrive?

wernerdaehn, 2024-06-07:
Best starting point is the source code for now.
https://github.com/wernerdaehn/CC3D-CableCam-Controller/blob/master/src/odrive.c

Yes, it is connected just like the VESC via UART.

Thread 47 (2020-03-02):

PWM frequency

litrosy, 2020-03-02:
Hi @wernerdaehn ,
I changed a new ESC that can operate at 48V. When I connect everything as it was on the previous 24V system (and everything worked fine), nothing happens. The ESC does not respond at all.

The ESC manual says:
 "-PWM mode1: 0-100% PWM: You can use your own PWM controll signal from your PLC or
microprocessor. The minimum controll PWM frequency is 100Hz. The step resolution 1us. The
acceptable voltage level: 3.3-10V.

- PWM mode2: RC wirelles receiver input 1.5msec pulse for 0% duty cycle and 2.5msec pulse for
the 97% duty cycle."

Currently is $n 1500 20 800, but whichever else I put, it is not responding at all.  I was thinking that the problem is maybe in PWM frequency which is below the required minimum of 100Hz?
In "wired" Potentiometer or throttle mode, everithing is fine.

Any suggestions?

wernerdaehn, 2020-03-02:
I have seen non-responsive ESCs in those cases where the signal **at start** was not within the neutral range of the ESC. The mode2 text above says "1.5ms to 2.5ms". Wouldn't that indicate that the neutral position is 2ms? So $n 2000 20 480? I hope that works. It is a bit unusal.
https://github.com/wernerdaehn/CC3D-CableCam-Controller/blob/master/docs/Step%205a%20-%20Regular%20ESC.md

The mode1 sounds like a true phase-width-modulation. Which means a signal that consists of x ms ON and y ms OFF. x+y=constant and 10ms minimum. Either way, we do not support that. We support RC like pulse modulation, where every n ms a puls is sent with the length of p ms, where p is something between 0.5 and 2.0ms.
https://en.wikipedia.org/wiki/Servo_control

litrosy, 2020-03-02:
Thank you very much for your quick response.

The problem was exactly what you wrote. I don't know how I missed $ n2000 20 480.

Thanks for your time, you really do help a lot.

Closed 2020-03-02.

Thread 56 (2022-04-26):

Roller Wheel

Unyck, 2022-04-26:
I have a simple question, how do you manage to drill the in line wheels properly ?  The polyurethane is slippy i try to attach it in a vice below a drill press but the materiel escape the wick.
If you have any advice about that

wernerdaehn, 2022-04-26:
I have created a fixed axis as holder and then drilled with the CNC mill/lathe the holes.

Unyck, 2022-04-30:
I read on one of your YouTube channel than you also use hard material wheels, I try on really soft one, it might be why I struggle.
Do you talk somewhere what is the size of the rope you use, I think about 8 or 12mm
Also I like to know the material of the spacer do you use nylon or aluminum ?
I can ask somewhere else if needed, glad you respond to me so fast, I really appreciate all of your work

Closed 2022-06-16.

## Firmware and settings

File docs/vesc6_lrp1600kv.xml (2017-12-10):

<?xml version="1.0" encoding="UTF-8"?>
<MCConfiguration>
    <foc_encoder_ratio>7</foc_encoder_ratio>
    <motor_quality_magnets>0</motor_quality_magnets>
    <foc_motor_flux_linkage>0.001848</foc_motor_flux_linkage>
    <l_temp_fet_end>100</l_temp_fet_end>
    <hall_table_5>6</hall_table_5>
    <p_pid_kd>0.0004</p_pid_kd>
    <m_encoder_counts>8192</m_encoder_counts>
    <l_erpm_start>0.8</l_erpm_start>
    <foc_duty_dowmramp_kp>10</foc_duty_dowmramp_kp>
    <foc_observer_gain_slow>0.3</foc_observer_gain_slow>
    <hall_table_7>-1</hall_table_7>
    <hall_table_4>5</hall_table_4>
    <foc_hall_table_5>82</foc_hall_table_5>
    <cc_ramp_step_max>0.04</cc_ramp_step_max>
    <sl_min_erpm>150</sl_min_erpm>
    <foc_sl_erpm>2500</foc_sl_erpm>
    <hall_table_6>4</hall_table_6>
    <m_dc_f_sw>35000</m_dc_f_sw>
    <foc_pll_ki>40000</foc_pll_ki>
    <comm_mode>0</comm_mode>
    <p_pid_ang_div>1</p_pid_ang_div>
    <l_current_max>60</l_current_max>
    <motor_poles>4</motor_poles>
    <l_max_erpm>100000</l_max_erpm>
    <m_current_backoff_gain>0.5</m_current_backoff_gain>
    <l_temp_motor_start>85</l_temp_motor_start>
    <foc_encoder_inverted>0</foc_encoder_inverted>
    <hall_table_3>2</hall_table_3>
    <foc_openloop_rpm>400</foc_openloop_rpm>
    <l_min_erpm>-100000</l_min_erpm>
    <foc_hall_table_4>52</foc_hall_table_4>
    <foc_hall_table_0>255</foc_hall_table_0>
    <motor_model>Not Specified</motor_model>
    <s_pid_kp>0.004</s_pid_kp>
    <motor_sensor_type>1</motor_sensor_type>
    <m_sensor_port_mode>0</m_sensor_port_mode>
    <foc_current_ki>9.52</foc_current_ki>
    <m_duty_ramp_step>0.02</m_duty_ramp_step>
    <foc_sl_d_current_duty>0</foc_sl_d_current_duty>
    <m_bldc_f_sw_min>3000</m_bldc_f_sw_min>
    <foc_current_kp>0.0024</foc_current_kp>
    <sl_cycle_int_limit>62</sl_cycle_int_limit>
    <s_pid_min_erpm>300</s_pid_min_erpm>
    <foc_observer_gain>2.9282e+8</foc_observer_gain>
    <cc_startup_boost_duty>0.01</cc_startup_boost_duty>
    <hall_table_0>-1</hall_table_0>
    <l_min_vin>8</l_min_vin>
    <foc_hall_table_3>146</foc_hall_table_3>
    <hall_table_2>3</hall_table_2>
    <sl_cycle_int_rpm_br>80000</sl_cycle_int_rpm_br>
    <sl_bemf_coupling_k>600</sl_bemf_coupling_k>
    <foc_duty_dowmramp_ki>200</foc_duty_dowmramp_ki>
    <l_max_erpm_fbrake>300</l_max_erpm_fbrake>
    <p_pid_kp>0.03</p_pid_kp>
    <sl_max_fullbreak_current_dir_change>10</sl_max_fullbreak_current_dir_change>
    <hall_table_1>1</hall_table_1>
    <foc_sat_comp>0</foc_sat_comp>
    <motor_quality_construction>0</motor_quality_construction>
    <foc_sample_high_current>0</foc_sample_high_current>
    <foc_sl_openloop_hyst>0.1</foc_sl_openloop_hyst>
    <l_in_current_max>60</l_in_current_max>
    <l_watt_min>-15000</l_watt_min>
    <foc_sl_openloop_time>0.1</foc_sl_openloop_time>
    <foc_sensor_mode>2</foc_sensor_mode>
    <sensor_mode>2</sensor_mode>
    <sl_phase_advance_at_br>0.8</sl_phase_advance_at_br>
    <l_temp_accel_dec>0.15</l_temp_accel_dec>
    <l_watt_max>15000</l_watt_max>
    <m_ntc_motor_beta>3380</m_ntc_motor_beta>
    <motor_loss_torque>0.03</motor_loss_torque>
    <foc_sl_d_current_factor>0</foc_sl_d_current_factor>
    <foc_encoder_offset>180</foc_encoder_offset>
    <foc_dt_us>0.08</foc_dt_us>
    <l_slow_abs_current>1</l_slow_abs_current>
    <foc_hall_table_2>177</foc_hall_table_2>
    <l_temp_motor_end>100</l_temp_motor_end>
    <hall_sl_erpm>2000</hall_sl_erpm>
    <l_max_duty>0.95</l_max_duty>
    <m_drv8301_oc_adj>16</m_drv8301_oc_adj>
    <foc_motor_l>2.37e-6</foc_motor_l>
    <motor_weight>0</motor_weight>
    <foc_temp_comp_base_temp>25</foc_temp_comp_base_temp>
    <cc_gain>0.0046</cc_gain>
    <l_max_erpm_fbrake_cc>1500</l_max_erpm_fbrake_cc>
    <l_battery_cut_start>10.2</l_battery_cut_start>
    <foc_temp_comp>0</foc_temp_comp>
    <motor_brand>Unnamed</motor_brand>
    <m_invert_direction>0</m_invert_direction>
    <l_temp_fet_start>85</l_temp_fet_start>
    <foc_hall_table_6>16</foc_hall_table_6>
    <s_pid_ki>0.004</s_pid_ki>
    <motor_description>&lt;!DOCTYPE HTML PUBLIC &quot;-//W3C//DTD HTML 4.0//EN&quot; &quot;http://www.w3.org/TR/REC-html40/strict.dtd&quot;&gt;
&lt;html&gt;&lt;head&gt;&lt;meta name=&quot;qrichtext&quot; content=&quot;1&quot; /&gt;&lt;style type=&quot;text/css&quot;&gt;
p, li { white-space: pre-wrap; }
&lt;/style&gt;&lt;/head&gt;&lt;body style=&quot; font-family:'DejaVu Sans'; font-size:11pt; font-weight:400; font-style:normal;&quot;&gt;
&lt;p style=&quot; margin-top:0px; margin-bottom:0px; margin-left:0px; margin-right:0px; -qt-block-indent:0; text-indent:0px;&quot;&gt;A motor description can be edited here.&lt;/p&gt;&lt;/body&gt;&lt;/html&gt;</motor_description>
    <motor_quality_bearings>0</motor_quality_bearings>
    <l_min_duty>0.005</l_min_duty>
    <motor_type>2</motor_type>
    <l_current_min>-60</l_current_min>
    <foc_motor_r>0.0095</foc_motor_r>
    <l_battery_cut_end>9.3</l_battery_cut_end>
    <m_bldc_f_sw_max>40000</m_bldc_f_sw_max>
    <motor_quality_description>&lt;!DOCTYPE HTML PUBLIC &quot;-//W3C//DTD HTML 4.0//EN&quot; &quot;http://www.w3.org/TR/REC-html40/strict.dtd&quot;&gt;
&lt;html&gt;&lt;head&gt;&lt;meta name=&quot;qrichtext&quot; content=&quot;1&quot; /&gt;&lt;style type=&quot;text/css&quot;&gt;
p, li { white-space: pre-wrap; }
&lt;/style&gt;&lt;/head&gt;&lt;body style=&quot; font-family:'DejaVu Sans'; font-size:11pt; font-weight:400; font-style:normal;&quot;&gt;
&lt;p style=&quot; margin-top:0px; margin-bottom:0px; margin-left:0px; margin-right:0px; -qt-block-indent:0; text-indent:0px;&quot;&gt;Some comments about the motor quality. Images can be added as well.&lt;/p&gt;&lt;/body&gt;&lt;/html&gt;</motor_quality_description>
    <sl_min_erpm_cycle_int_limit>1100</sl_min_erpm_cycle_int_limit>
    <m_fault_stop_time_ms>500</m_fault_stop_time_ms>
    <l_max_vin>57</l_max_vin>
    <foc_sample_v0_v7>1</foc_sample_v0_v7>
    <foc_hall_table_1>117</foc_hall_table_1>
    <p_pid_ki>0</p_pid_ki>
    <pwm_mode>1</pwm_mode>
    <s_pid_allow_braking>1</s_pid_allow_braking>
    <foc_pll_kp>2000</foc_pll_kp>
    <l_abs_current_max>150</l_abs_current_max>
    <foc_f_sw>20000</foc_f_sw>
    <foc_hall_table_7>255</foc_hall_table_7>
    <s_pid_kd>0.0001</s_pid_kd>
    <l_in_current_min>-40</l_in_current_min>
    <cc_min_current>0.1</cc_min_current>
    <m_drv8301_oc_mode>0</m_drv8301_oc_mode>
</MCConfiguration>

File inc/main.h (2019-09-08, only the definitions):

#define LED_WARN_ON HAL_GPIO_WritePin(GPIOB, GPIO_PIN_4, GPIO_PIN_RESET)
#define LED_WARN_OFF HAL_GPIO_WritePin(GPIOB, GPIO_PIN_4, GPIO_PIN_SET)
#define LED_WARN_TOGGLE HAL_GPIO_TogglePin(GPIOB, GPIO_PIN_4)
#define LED_STATUS_ON HAL_GPIO_WritePin(GPIOB, GPIO_PIN_5, GPIO_PIN_RESET)
#define LED_STATUS_OFF HAL_GPIO_WritePin(GPIOB, GPIO_PIN_5, GPIO_PIN_SET)
#define LED_STATUS_TOGGLE HAL_GPIO_TogglePin(GPIOB, GPIO_PIN_5)

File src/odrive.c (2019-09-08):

#include "odrive.h"
#include "stdio.h"
#include "string.h"
#include "serial_print.h"
#include "protocol.h"
#include "clock_50hz.h"
#include "math.h"
#include "uart_callback.h"

void ODRIVE_set_rpm(int32_t odrive_erpm);
void ODRIVE_set_position(float target_pos);
void ODRIVE_Request_Value(ODRIVE_REQUEST_t requesttype);
int32_t getODriveIntValue(void);
float getODriveFloatValue(void);

uint8_t odriveTxBuffer[UART_CYCLIC_RXBUFFER_SIZE];

uint32_t last_odrive_read_request;
ODRIVE_REQUEST_t odriverequested = ODRIVE_REQUESTED_NONE;
ODRIVE_REQUEST_t odrivecurrentvalue = ODRIVE_REQUESTED_NONE;

uint16_t odrive_received_pos = 0;
uint16_t odrive_packet_start_pos = 0;
uint32_t odrive_bytes_written = 0;
uint32_t odrive_bytes_sent = 0;

uint8_t odrive_cyclic_rxbuffer[UART_CYCLIC_RXBUFFER_SIZE];
uint8_t odrive_rxbuffer[UART_CYCLIC_RXBUFFER_SIZE];
uint32_t odrive_last_data_timestamp = 0;

ODRIVE_STATUS_t odrivestatus;
uint16_t counter = 0;

extern UART_HandleTypeDef huart2;

void ODRIVE_init()
{
    controllerstatus.odrivestate = ODRIVE_UNKNOWN;
    if(HAL_UART_Receive_DMA(&huart2, odrive_cyclic_rxbuffer, UART_CYCLIC_RXBUFFER_SIZE) != HAL_OK)
    {
        Error_Handler();
    }
}

void ODRIVE_Output(float esc_output)
{

    switch (controllerstatus.odrivestate)
    {
    case ODRIVE_MOTOR_TO_BE_CALIBRATED:
    case ODRIVE_UNKNOWN:
        if (odrivecurrentvalue != ODRIVE_REQUESTED_MOTOR_CALIBRATED || odrivestatus.motor_calibrated  != 1)
        {
            if (odrivecurrentvalue == ODRIVE_REQUESTED_MOTOR_CALIBRATED)
            {
                PrintlnSerial_string("oDrive motor is NOT calibrated, see oDrive manual on how to do that and store the setting permanently", EndPoint_All);
            }
            ODRIVE_Request_Value(ODRIVE_REQUESTED_MOTOR_CALIBRATED);
        }
        else
        {
            if (odrivestatus.motor_calibrated  == 1)
            {
                controllerstatus.odrivestate = ODRIVE_MOTOR_CALIBRATED;
                PrintlnSerial_string("oDrive motor is calibrated", EndPoint_All);
            }
        }
        break;
    case ODRIVE_MOTOR_CALIBRATED:
        if (odrivecurrentvalue != ODRIVE_REQUESTED_ENCODER_CALIBRATED || odrivestatus.encoder_calibrated != 1)
        {
            ODRIVE_Request_Value(ODRIVE_REQUESTED_ENCODER_CALIBRATED);
        }
        else
        {
            if (odrivestatus.encoder_calibrated == 1)
            {
                controllerstatus.odrivestate = ODRIVE_ENCODER_CALIBRATED;
                PrintlnSerial_string("oDrive encoder is calibrated", EndPoint_All);
            }
        }
        break;
    case ODRIVE_ENCODER_CALIBRATED:
        if (odrivecurrentvalue != ODRIVE_REQUESTED_CLOSED_LOOP || odrivestatus.closed_loop != 8)
        {
            ODRIVE_Request_Value(ODRIVE_REQUESTED_CLOSED_LOOP);
        }
        else
        {
            if (odrivestatus.closed_loop == 8)
            {
                controllerstatus.odrivestate = ODRIVE_SPEED_MODE;
                PrintlnSerial_string("oDrive is in speed mode", EndPoint_All);
            }
        }
        break;
    case ODRIVE_SPEED_MODE:
        if (odrivecurrentvalue != ODRIVE_REQUESTED_SPEED_CONTROL_MODE)
        {
            ODRIVE_Request_Value(ODRIVE_REQUESTED_SPEED_CONTROL_MODE);
        }
        else
        {
            if (odrivestatus.speed_control_loop ==  2) // 2...velocity control
            {
                controllerstatus.odrivestate = ODRIVE_CLOSED_LOOP;
                PrintlnSerial_string("oDrive is in closed loop operation (velocity control)", EndPoint_All);
            }
            else if (odrivestatus.speed_control_loop ==  3) // 3...position control
            {
                controllerstatus.odrivestate = ODRIVE_CLOSED_LOOP;
                activesettings.pos_source = 1;
                PrintlnSerial_string("oDrive is in closed loop operation (position control)", EndPoint_All);
            }
        }
        break;
    case ODRIVE_CLOSED_LOOP:
        if (odrivecurrentvalue != ODRIVE_REQUESTED_SPEED_LIMIT)
        {
            ODRIVE_Request_Value(ODRIVE_REQUESTED_SPEED_LIMIT);
        }
        else
        {
            float p = getODriveFloatValue();
            PrintSerial_string("oDrive has a max speed of ", EndPoint_All);
            PrintSerial_float(p, EndPoint_All);
            PrintSerial_string(" and this controller of ", EndPoint_All);
            PrintlnSerial_float(activesettings.esc_max_speed, EndPoint_All);
            if (p < activesettings.esc_max_speed) // if the programmed speed is higher than the hard limit set in the odrive, use this
            {
                activesettings.esc_max_speed = p;
            }
            controllerstatus.esc_max_speed = activesettings.esc_max_speed; // controllerstatus contains the read value
            controllerstatus.odrivestate = ODRIVE_OPERATIONAL;
        }
        break;
    case ODRIVE_OPERATIONAL:
        if (is5s())
        {
            switch (counter)
            {
                case 0: ODRIVE_Request_Value(ODRIVE_REQUESTED_ERRORCODE); break;
                case 1: ODRIVE_Request_Value(ODRIVE_REQUESTED_ERRORCODEMOTOR); break;
                case 2: ODRIVE_Request_Value(ODRIVE_REQUESTED_ERRORCODECONTROLLER); break;
                case 3: ODRIVE_Request_Value(ODRIVE_REQUESTED_ERRORCODEENCODER); break;
            }
            counter++;
            if (counter > 3)
            {
                counter = 0;
            }
        }
        else if (is5Hz())
        {
            ODRIVE_Request_Value(ODRIVE_REQUESTED_POSITION);
        }

        if (activesettings.pos_source == 1)
        {
            ODRIVE_set_position(controllerstatus.target_pos);
        }
        else if (isnan(esc_output))
        {
            ODRIVE_set_rpm(0);
        }
        else
        {
            int32_t odrive_speed;
            if (activesettings.mode == MODE_PASSTHROUGH)
            {
                odrive_speed = (int32_t) ((esc_output * ((float) activesettings.esc_max_speed)));
            }
            else
            {
                // controllerstatus.stick_max_speed reduces the vesc erpm by this factor at stick=100%
                odrive_speed = (int32_t) ((esc_output * controllerstatus.stick_max_speed * ((float) activesettings.esc_max_speed)));
            }
            ODRIVE_set_rpm(odrive_speed);
        }

    }
}

void ODRIVE_set_rpm(int32_t odrive_speed)
{
    char buf[40];
    if (odrive_speed > activesettings.esc_max_speed)
    {
        odrive_speed = activesettings.esc_max_speed;
    }
    else if (odrive_speed < -activesettings.esc_max_speed)
    {
        odrive_speed = -activesettings.esc_max_speed;
    }
    uint32_t len = snprintf(buf, sizeof(buf), "v 0 %ld 0\n", odrive_speed);
    if (len > 0)
    {
        ODRIVESendPacket((uint8_t *) buf, len);
    }
}
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

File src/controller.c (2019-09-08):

#include "config.h"
#include "protocol.h"
#include "controller.h"
#include "protocol.h"
#include "clock_50Hz.h"
#include "sbus.h"
#include "vesc.h"
#include "math.h"
#include "eeprom.h"
#include "odrive.h"

extern getvalues_t vescvalues;

void printControlLoop(int16_t input, float speed, float pos, float brakedistance, uint16_t esc, Endpoints endpoint);
float stickCycle(void);
float getStickPositionRaw(void);
float abs_d(float v);
void printBrakeMessage(float value, float brakedistance, float speed, uint8_t type, Endpoints endpoint);
void evalute_stick_programming_mode(float value);
void evalute_stick_endpoint_switch(void);
void evalute_stick_accel_dial(void);
void evalute_stick_speed_dial(void);
void evalute_stick_mode_switch(void);
void evalute_stick_play_switch(void);
void set_next_targetpos(float v0, float accel);

/*
 * Preserve the previous filtered stick value to calculate the acceleration
 */
float stick_last_value = 0.0f;
float last_pos = 0.0f;

static float stickintegral = 0.0f;


uint8_t endpointclicks = 0;
float lastendpointswitch = 0.0f;
uint8_t lastmodeswitchsetting = 255;

float gimbalout[8];



float getStick(void)
{
    return stick_last_value;
}

void setPos(void)
{
    int32_t v;

    /*
     * Depending on the setting, either the VESC Tacho is used or the encoder.
     */
    if (activesettings.pos_source == 1)
    {
        if (activesettings.esc_type == ESC_VESC)
        {
            // The pos sensor value comes from the VESC internal tachometer
            v = vesc_get_long(vescvalues.frame.tachometer); // Convert uint to int
        }
        else
        {
            if (activesettings.pos_source == 1)
            {
                v = controllerstatus.target_pos;
            }
            else
            {
                v = controllerstatus.odrive_pos;
            }
        }
    }
    else
    {
        // The pos sensor value is created by the external sensor
        v = ENCODER_VALUE; // Convert uint to int
    }

    /*
     * Deal with the esc_direction setting, which can be +1, -1 or unknown, in which case +1 is assumed
     */
    if (activesettings.esc_direction == 0.0f)
    {
        controllerstatus.pos = (float) v;
    }
    else
    {
        controllerstatus.pos =  ((float) v) * activesettings.esc_direction;
    }

    /*
     * In order to deal with pos changes below 1 per controller cycle, the controller status structure holds
     * the time when the position did change the last time.
     *
     * Example: current time = 1; last_change_time = 0; position did change by 2; --->  speed = 2.
     * Example: current time = 5; last_change_time = 0; position did change by 1; --->  speed = 1/5.
     *
     */
    uint32_t current_cycle_counter = getCounter(); // Get the number of 20ms intervals
    if (controllerstatus.pos != last_pos)
    {
        uint32_t time_diff = current_cycle_counter - controllerstatus.last_pos_change;
        controllerstatus.pos_diff = controllerstatus.pos - last_pos;
        controllerstatus.speed_by_posdiff = abs_d(controllerstatus.pos_diff / ((float) time_diff ));
        controllerstatus.last_pos_change = current_cycle_counter;

        last_pos = controllerstatus.pos;
    }
    else if (current_cycle_counter - controllerstatus.last_pos_change > 25L)
    {
        /*
         * In case the position did not change for 0.5 seconds, a speed=0 is assumed.
         */
        controllerstatus.speed_by_posdiff = 0.0f;
        controllerstatus.pos_diff = 0.0f;
        last_pos = controllerstatus.pos;
    }

    //
    // If the encoder is used, then there is a more accurate way to calculate the speed, that is measuring the time using
    // the hardware interrupt (input capture) of the encoder. This has a higher precision than 0.02 seconds.
    //
    // Speed is the number of signals per 0.02 (=Ta) secs.
    // Hence refactor Ta to milliseconds to match the HAL_GetTick() millisecond time scale.
    // The encoder is set to by an X4 type and increases on falling and raising flanks
    // whereas the interrupt fires on one pin and rising flank - hence times 4.
    //
    if (activesettings.pos_source != 1)
    {
        uint32_t timesincelastpostick = HAL_GetTick() - controllerstatus.last_possensortick;
        /*
         * In case the position did not change for 0.5 seconds, a speed=0 is assumed.
         */
        if (controllerstatus.possensorduration == 0 || timesincelastpostick > 500L)
        {
            //
            // Failsafe for below's division.
            //
            controllerstatus.speed_by_time = 0.0f;
        }
        else
        {
            if (timesincelastpostick > 300)
            {
                // The speed between ticks only works if the wheel is moving. Else the speed should continue to decline.
                controllerstatus.possensorduration+= CONTROLLERLOOPTIME_MS;
            }
            controllerstatus.speed_by_time = CONTROLLERLOOPTIME_FLOAT * 1000.0f * 4.0f / ((float) controllerstatus.possensorduration);
        }
    }
}

void initController(void)
{
    controllerstatus.safemode = INVALID_RC;
    controllerstatus.play_running = FORCE_OFF;
    controllerstatus.possensorduration = 0;
    controllerstatus.last_possensortick = 0;
}

float abs_d(float v)
{
    if (v < 0.0f)
    {
        return -v;
    }
    else
    {
        return v;
    }
}

float getProgrammingSwitch()
{
    return getDuty(activesettings.rc_channel_programming);
}

float getEndPointSwitch()
{
    return getDuty(activesettings.rc_channel_endpoint);
}

float getMaxAccelPoti()
{
    return getDutyIgnoreNeutral(activesettings.rc_channel_max_accel);
}

float getMaxSpeedPoti()
{
    return getDutyIgnoreNeutral(activesettings.rc_channel_max_speed);
}

float getModeSwitch()
{
    return getDuty(activesettings.rc_channel_mode);
}

float getPlaySwitch()
{
    return getDuty(activesettings.rc_channel_play);
}

float getAuxInput()
{
    return getDuty(activesettings.rc_channel_aux);
}
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

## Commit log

2017-06-17 Initial Branch for the new CC3D Revolution based Firmware
    [Sensorboard.3dm, Sensorboard.dwg, Sensorboard.dxf]
2017-08-15 Fix of end limiter and added ESC Neutral pos and range.
    [controller.c, main.h, protocol.c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]
2017-08-16 ESC Debug Info
2017-08-16 ESC output
2017-08-16 ESC output update
2017-08-17 Fixes for the End point brake
    [controller.c, protocol.c]
2017-08-18 Added the brake logic in case an open loop ESC is used. Rewrote the USB string receiver.
2017-08-20 sbus.c file was missing
    [sbus.c]
2017-08-20 A few fixes identified when on the rope.
    [controller.c, protocol.c]
2017-12-09 VESC UART support
2017-12-09 rebuilt image for VESC support
2017-12-10 Added vesc6 config files for reference.
    [vesc6_lrp1600kv.xml]
2017-12-25 VESC with handbrake, more status change messages
2018-02-11 Added bluetooth functionality plus cleanup of the serialprint. It reacts on \n chars only not as before on \r or \n. That became necessary because the code did return \r and \n to the console out of 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
    [bluetooth.c, controller.c, protocol.c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]
2018-02-17 Solved a couple of minor issues. $E to read the VESC6 status
    [main.h, protocol.c, protocol.h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]
2018-02-17 printdouble had a formatting issue
    [protocol.c]
2018-02-18 VESC UART to actual values conversion was wrong due to order of big/little endian and uint/int conversion in the wrong order.
    [controller.c, protocol.c, vesc.c]
2018-02-23 Updated $c command, automatic setting of $r in case it is unset yet.
2018-02-28 Minor error corrections and updated the docs a bit for $1 and bluetooth description.
    [controller.c, main.h, protocol.c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]
2018-03-07 Correction of the ESC Neutral command. https://github.com/wernerdaehn/CC3D-CableCam-Controller/issues/12
    [controller.c, protocol.c]
2018-03-25 Max Accel via Poti increased the range value. Before it allowed a value of $a from 0.05 to 0.5, now it is 0.05 to 1.0. $i has one more input for the Aux output. Simple pass through.
    Example: $i 8 11 12 9 10 7 2
    This sets the Input Channel #2 as input for the Aux Channel. And this value, rescaled to PPM is output in Servo2.
2018-04-02 Added a Play function, changes in the commands and their return, e.g. $h, $S, $i decimals are formatted with less leading spaces PC6 should output a non-inverted SBus signal meant for the gimbal, see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
    [CableCam Controller.ioc, controller.c, protocol.c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]
2018-04-04 Changed the scaling of the speed and accel poti. Before the scale was fixed, not it controls the percentage of the defined $a and $v. So with both potis at +100% you would reach exactly that accel/sp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
    [controller.c, protocol.c, protocol.h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]
2018-04-22 Changed the handling of max_speed. No longer controls the max stick input but rather controls how much output the 100% stick is. Added $V for version.
    [controller.c, protocol.c, protocol.h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]
2018-05-19 Fix in the Play function when esx_direction = -1 When second endpoint is set, then the endpoints are saved in sector #3 in eeprom.
    [controller.c, eeprom.c, protocol.c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]
2018-05-19 Added an error condition when $r=0 and the second end point is set. The code tries to guess the correct $r setting then but for this it needs stick movement. If the cablecam was pulled by hand....wri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
    [controller.c]
2018-05-23 Fix for $g handling
    [controller.c]
2018-06-27 Fixed issues #21 (Problem with mode switch, mid setting too narrow) #22, Part 2 ($i 1 2 3 4 5 6 7 8 with followed $i 1 2 3 4 5 6 256 256 does nto disable the last two channels)
    [controller.c, protocol.c]
2018-07-09 Change for the Futaba Receiver, no longer testing the end byte value.
    [sbus.c, timer_callbacks.c]
2018-07-22 #24 #25 Defaults not used, more failsafes around play, fix play via app
    [controller.c, protocol.c, protocol.h]
2018-08-20 Docs for the Vesc config
2018-09-12 Rework IO, HAL Layer and more
    [controller.c, protocol.c, protocol.h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]
2018-09-15 Added an endpoint offset and stabilized the communication
    [CableCam Controller.ioc, controller.c, protocol.c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]
2019-01-25 First cut of odrive support
2019-02-02 New SumPPM interrupt implementation
2019-03-24 optimizing the odrive $1 setup wizard is broken at the moment
    [odrive.c, protocol.c, protocol.h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]
2019-09-08 Update odrive for positional control

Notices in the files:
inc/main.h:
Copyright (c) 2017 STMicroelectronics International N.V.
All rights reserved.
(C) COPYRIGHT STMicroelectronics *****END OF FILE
